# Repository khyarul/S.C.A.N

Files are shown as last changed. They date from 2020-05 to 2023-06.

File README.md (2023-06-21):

# S.C.A.N
 Small and Cheap Attendance Node

## Attendance Node Machine
   - Hardware: ESP8266 Wemos D1 Mini - Software: Arduino C/C++

   - Feature and library used:
     - [x] Dual Mode: **Tap to Unlock Door** and **Attendance Mode**
     - [x] Scheduler.h (Multitask) from [Here](https://github.com/nrwiersma/ESP8266Scheduler)
     - [x] PubSubClient.h (MQTT protocol client)
     - [x] LiquidCrystal_I2C.h (LCD16x2 I2C)
     - [x] MFRC522.h (RFID SPI module 13.56MHz)
     - [x] ArduinoOTA.h (wireless/no-usb programming)
     - [x] Reed/magnetic sensor for Door state
     - [x] solenoid door lock port max. 12V/1A (12W)
     - [x] 5V/3A (15W) power supply input
   
   - Recommended ESP8266 Wemos D1 Mini Arduino Configuration:
   
   arduino config
 
   - Wemos D1 Mini Port Allocation:
   
 PORT |	FUNCTION |	DEVICE
 -----|----------|-------   
 D1 |	I2C SCL |	LCD 16x2
 D2 |	I2C SDA |	LCD 16x2
 D4 |	SPI Reset |	RC522
 D5 |	SPI SCK |	RC522
 D6 |	SPI MISO |	RC522
 D7 |	SPI MOSI	| RC522
 D8 |	SPI SS	| RC522
 D0 |	Digital Output	| Solenoid
 TX |	Digital Input	| Attendance Mode button
 RX |	Digital Output |	Buzzer
 D3 |	Digital Input |	“Unlock Door” Mode button
 A0 |	Analog Input |	Magnetic Switch/Sensor

   - Mechanic Documentation Photo:
     - **Acrylic Case for LCD, RFID sensor, button, and buzzer. Install it outside the room.**



     - **Acrylic case for controller part, reed/magnet sensor and solenoid port. Install it inside the room.**


     - **Solenoid port and small hole for reed/magnet sensor wire**



   
## GUI (Node Monitor & Employee Manager)
- Tested on Windows 10 PC and Ubuntu Mate 18.04 64bit on Raspberry Pi 3 (Should be supported with Ubuntu 64bit on PC)
- Main file: **"SCAN_node_monitor.py"** (**"karyawan.py"**, **"icons"**, and **"images" need to be in the same folder**)

- Feature:
  - [x] Manage & monitor all Node Machine that connected to the same MQTT server.
  - [x] Using MongoDB database for Node & Employee Manager.
  - [x] Unlock door on every Node Machine remotely.

- Python 3.7 module/library used:
  - [x] Pyqt5 (for GUI)
  - [x] PyMongo (for MongoDB Database driver)
  - [x] Paho-Mqtt (MQTT client)
  - [x] Threading (Multitasking using Multithreading, 1 thread per 1 Attendance Node Machine)

## Support & DONATE this open source project:
  - PAYPAL  : [SentinelCreative](https://www.paypal.me/sentinelcreative "PAYPAL")
  - BNI     : 1284959883 (Khyarul Arham)
  - Jago    : 504120557241 (Khyarul Arham)

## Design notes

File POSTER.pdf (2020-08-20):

# PENERAPAN MOSQUITTO SEBAGAI SERVER MQTT LOKAL PADA KOMUNIKASI ANTARA DATABASE MONGODB DAN MESIN ABSENSI MULTI-NODE

1. Menerapkan protokol MQTT pada mesin absensi di local area network dengan mengandalkan access point terdekat untuk komunikasi lebih handal dan aman.
2. Menerapkan algoritma komunikasi bidirectional dari protokol MQTT pada perangkat-perangkat yang terhubung pada jaringan lokal atau jaringan publik.
3. Menggunakan aplikasi GUI designer PyQt5 dan penerapannya untuk menginput, mengedit, dan menampilkan data dari suatu database dengan konsep NoSQL salah satunya MongoDB dengan library PyMongo pada Python serta sebagai penerapan manajemen database secara terpusat.
4. Menganalisa pengaruh penggunaan server MQTT (lokal dan publik), proses parsing data pada Python dan update pada database MongoDB, serta penambahan jumlah client terhadap delay pada sistem.

Mesin absensi di pasaran rata-rata hanya menggunakan sistem standalone database, yaitu 1 database untuk 1 mesin walaupun sudah menerapkan prinsip IoT. Salah satu protokol yang sering digunakan dalam IoT saat ini salah satunya protokol MQTT. Protokol MQTT sudah sering dijadikan pembahasan, namun masih memanfaatkan public MQTT Server yang sudah siap pakai dan kebanyakan hanya dilakukan untuk komunikasi 1 arah. Public MQTT broker harus menggunakan internet walaupun hanya untuk perangkat yang letaknya tidak terlalu jauh. Komunikasi antar client dengan cloud broker akan terganggu bila koneksi internet mengalami gangguan terutama instansi yang berada di daerah yang belum dijangkau oleh ISP yang handal. Untuk mengatasinya perlu menerapkan MQTT menggunakan jaringan lokal yang sudah tersedia tanpa memerlukan internet. Dengan menerapkan protokol MQTT secara lokal dan komunikasi dua arah, PyQt serta MongoDB sebagai manajemen database terpusat diharapkan mempermudah dalam memonitor dan mengatur jumlah mesin absensi yang terkoneksi.

Urutan kerja sistem autentikasi dari Client Node ke Client Database, yaitu:
1. User melakukan tapping RFID tag pada mesin client node. Mesin akan mengirimkan UID ke server MQTT melalui topik khusus UID dan unique client ID dari node bersangkutan.
2. Client database akan mendeteksi payload yang masuk di topik tersebut. Dengan syarat client database sudah berlangganan ke topik tersebut.
3. Data yang diterima oleh client database akan dilakukan parsing serta pengecekan ke database MongoDB.
4. Client database akan mengirim respon balik ke server MQTT sesuai topik dari client ID node yang bersangkutan apakah UID user memiliki akses atau tidak.
5. Client node akan menampilkan output dan respon ke user berdasarkan payload respon yang sudah diterima oleh client node.
- Local MQTT Server
1. Hardware: Raspberry Pi 3 Model B V1.2
2. Sistem Operasi: Ubuntu Mate 18.04.4 LTS 64bit
- Monitor dan Database Client
1. Hardware: Raspberry Pi 3 Model B V1.2
2. Sistem Operasi: Ubuntu Mate 18.04.4 LTS 64bit
3. Bahasa Pemrograman: Python 3.6
4. GUI: PyQt5
5. Database: MongoDB V4.2
6. Database library: Pymongo
7. MQTT Client library: Paho-Mqtt
- Node Client
1. Hardware: ESP8266 Wemos D1 Mini
2. Bahasa Pemrograman: Arduino C/C++
TUJUAN | LATAR BELAKANG
CARA KERJA ALAT | SPESIFIKASI ALAT | BLOK DIAGRAM HARDWARE NODE CLIENT
FLOWCHART SISTEM AUTENTIKASI | BLOK DIAGRAM SISTEM KOMUNIKASI

### Dibuat Oleh: Khiarul Arham

(1903423002)

### Dosen Pembimbing:

Agus Wagyana, S.T., M.T.
(196808241999031002)

### Tanggal Sidang: 28 Juli 2020

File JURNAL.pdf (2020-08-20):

PENERAPAN MOSQUITTO SEBAGAI SERVER MQTT LOKAL PADA KOMUNIKASI ANTARA DATABASE MONGODB DAN MESIN ABSENSI MULTI-NODE Khiarul Arham, Agus Wagyana Politeknik Negeri Jakarta, Jurusan Teknik Elektro, Prodi Broadband Multimedia Jl. Prof. Dr. G. A. Siwabessy, Kampus UI, Depok 16425 email: kh.arham@gmail.com

ABSTRACT
Attendance machines on the market mostly only use a standalone database system, which is 1 database for 1 machine despite applying the IoT principle. One protocol that is often used in IoT is the MQTT protocol. The MQTT protocol has often been studied, but it still utilizes public MQTT Servers that are ready to use and most are only done for 1-way communication. Public MQTT brokers must use the internet even if only for devices that are not too far away. Communication between clients and public brokers will be disrupted if the internet connection is interrupted, especially agencies in areas that have not been reached by a reliable ISP. To overcome this, it is necessary to implement MQTT using a local network that is already available without the need for internet. By implementing the MQTT protocol locally and two-way communication, PyQt and MongoDB as a centralized database management are expected to make it easier to monitor and manage the number of connected attendance machines. The system applied in this study has 3 components, namely MQTT Server, Monitor and Database Client, and Node Client. To conduct two-way communication each client publishes and subscribes to specific topics based on the client ID. Next will be investigated the effect of 3 parameters, i.e. the type of MQTT server used, the number of client nodes, and the process of updating the database to the delay in the authentication process. Obtained the difference in delay between the application of local and public MQTT servers is 816.75 ms. Increasing the number of client nodes also affects the delay of about 135.75 ms for each addition of 1 node client. The process of updating the MongoDB database in Python has the least delay effect compared to 2 other parameters, which is only 68.75 ms.

Key words: Attendance; client monitor; client node; MongoDB; Mosquitto; MQTT; PyQt

ABSTRAK
Mesin absensi di pasaran rata-rata hanya menggunakan sistem standalone database, yaitu 1 database untuk 1 mesin walaupun sudah menerapkan prinsip IoT. Salah satu protokol yang sering digunakan dalam IoT saat ini salah satunya protokol MQTT. Protokol MQTT sudah sering dijadikan pembahasan, namun masih memanfaatkan public MQTT Server yang sudah siap pakai dan kebanyakan hanya dilakukan untuk komunikasi 1 arah. Public MQTT broker harus menggunakan internet walaupun hanya untuk perangkat yang letaknya tidak terlalu jauh. Komunikasi antar client dengan cloud broker akan terganggu bila koneksi internet mengalami gangguan terutama instansi yang berada di daerah yang belum dijangkau oleh ISP yang handal. Untuk mengatasinya perlu menerapkan MQTT menggunakan jaringan lokal yang sudah tersedia tanpa memerlukan internet.

Dengan menerapkan protokol MQTT secara lokal dan komunikasi dua arah, PyQt serta MongoDB sebagai manajemen database terpusat diharapkan mempermudah dalam memonitor dan mengatur jumlah mesin absensi yang terkoneksi. Sistem yang diterapkan pada penelitian ini memiliki 3 komponen, yaitu MQTT Server, Monitor dan Database Client, dan Node Client. Untuk melakukan komunikasi dua arah setiap client melakukan publish dan subscribe ke topik tertentu berdasarkan client ID. Selanjutnya akan dicari tahu pengaruh 3 parameter, yaitu jenis server MQTT yang digunakan, jumlah client node, dan proses update database terhadap delay dalam proses autentikasi. Didapatkan perbedaan delay antara penerapan server MQTT lokal dan publik adalah 816.75 ms. Bertambahnya jumlah client node juga mempengaruhi delay sekitar 135.75 ms setiap penambahan 1 client node. Proses update database MongoDB pada Python memiliki pengaruh delay paling kecil dibandingkan 2 paramater lain, yaitu hanya 68.75 ms.

Kata kunci: Attendance; client monitor; client node; MongoDB; Mosquitto; MQTT; PyQt

PENDAHULUAN
Sistem absensi seringkali menjadi
perhatian | sebuah | instansi | dalam
pengelolaan puluhan atau bahkan ratusan sumber daya manusia (karyawan), sehingga banyak perusahaan telah menerapkan sistem absensi digital. Kebanyakan instansi atau perusahaan memiliki gedung yang berdekatan atau hanya satu gedung, sehingga cukup meletakkan 1 atau 2 mesin absensi dengan pengumpulan data manual
menggunakan | flashdisk | tanpa | harus
mengintegrasikannya ke jaringan lokal instansi tersebut. Beda halnya dengan instansi dengan area yang luas dan jarak antar gedung yang cukup jauh, sehingga mengharuskan instansi tersebut memasang mesin absensi di masing-masing gedung tempat karyawan bekerja yang jumlahnya tidak sedikit. Tentunya sangat merepotkan untuk mengumpulkan data di tempat-tempat yang berjauhan secara manual untuk masing-masing mesin. Kalaupun masing-
masing | gedung | memiliki | seorang
perwakilan untuk mengumpulkan datanya, maka untuk menggabungkan semua data
tersebut | akan | merepotkan | bagian
administrasi bila dilakukan setiap hari atau setiap minggu.
Untuk mesin yang memiliki fitur logging ke jaringan sendiri masih terbilang cukup mahal dan rata-rata memiliki database yang terpisah (standalone), yang beredar di pasaran misalnya ZT1200 atau ZT1100 yang menggunakan MySQL sebagai standalone database. Bagi instansi sejenis pabrik, manufaktur, atau bisnis dengan kemampuan budget tinggi, itu bukanlah masalah besar. Namun untuk instansi non-bisnis dengan kemampuan budget menengah atau instansi pada umumnya, dan ditambah dengan area luas, hal itu benar-benar harus dipertimbangkan. Oleh karena itu masih banyak yang
menggunakan | cara | manual | untuk
perekapan data absensi.
| Sekarang | ini | dengan | adanya
perkembangan | sistem | integrasi | antar
perangkat dengan jaringan seperti Internet
of | Things | (IoT) | ditambah | dengan
penerapannya yang tidak hanya pada komputer atau perangkat jaringan pada umumnya. Begitu mudahnya sekarang ini dalam menemukan source code atau binary resource untuk berbagai macam protokol pendukung IoT yang disediakan untuk para hobby dan developer, salah satunya protokol Message Queiuing Telemetry Transport (MQTT). MQTT menjadi salah satu protokol yang banyak digunakan pada aplikasi IoT karena memiliki ukuran paket data yang kecil sehingga cocok digunakan pada aplikasi real-time atau aplikasi yang membutuhkan kemampuan data streaming yang baik. Dari beberapa info yang penulis dapatkan dari dosen dan referensi di internet, protokol MQTT sudah beberapa kali dijadikan bahan pembahasan untuk keperluan tugas akhir atau skripsi, namun masih memanfaatkan public cloud MQTT broker yang sudah siap pakai. Dalam penerapannya cloud MQTT broker harus menggunakan koneksi internet walaupun hanya untuk perangkat yang letaknya tidak
jauh | atau | berdekatan. | Tentu | akan
menghambat komunikasi antar | client
dengan cloud broker bila saat koneksi internet atau Internet Service Provider (ISP) yang sering mengalami gangguan terutama instansi yang berada di daerah tepencil atau masih belum dijangkau banyak ISP lain yang handal. Sehingga untuk mengatasinya agar lebih efisien perlu adanya penerapan MQTT yang cukup memanfaatkan jaringan lokal yang sudah tersedia di suatu instansi tanpa harus memakan bandwidth internet.
Salah | satu | penyedia | open-source
MQTT client & broker yaitu Eclipse
Mosquitto. | Dengan | menggunakan
Mosquitto kita dapat menerapkan protokol MQTT pada jaringan lokal. Mosquitto juga menyediakan binary yang mendukung berbagai macam sistem operasi seperti Windows, Linux, dan Mac. Bahkan Mosquitto juga dapat dipasang pada single board computer (SBC) seperti Raspberry Pi. Dengan memanfaatkan low power single board computer sebagai MQTT broker maka kita tidak perlu menggunakan sebuah Personal Computer (PC) yang harus standby selama koneksi dengan broker diperlukan terkait pertimbangan penggunaan daya. Selain itu output data dari client juga dapat ditampilkan pada sebuah database dengan merancang GUI pada SBC tersebut. Salah satu platform GUI yang dapat digunakan, yaitu Qt yang juga menyediakan tools designer untuk mempermudah developer saat merancang GUI dengan fitur konversi hasil desain ke
bahasa | pemrograman | seperti | C/C++
ataupun Python (PyQt).
Penerapan IoT dalam inovasi teknologi semakin menuntut adanya variasi data serta
fleksibilitas | dalam | mengakses | serta
menyimpan data. Banyak perusahaan besar di dunia seperti Facebook yang telah bermigrasi dan menerapkan database NoSQL salah satunya MongoDB. Salah satu fitur MongoDB adalah menyimpan data dalam bentuk JSON document. Sebagai programmer pada umumnya berpikir secara objek, dengan cara ini
MongoDB | mendekati | cara | berpikir
tersebut, sehingga lebih fleksibel dan handal dibandingkan database dengan pemodelan baris dan kolom seperti MySQL
dan | sejenisnya. | Dalam | akses
pemrogramannya, Python sangat cocok dipasangkan dengan MongoDB karena dalam Python memiliki tipe data dictionary yang sangat mirip dengan JSON. Ditambah dengan adanya library atau driver yang tersedia pada Python untuk mengakses MongoDB, yaitu PyMongo. Dengan begitu akan mempermudah dalam implementasi dan menggabungkannya pada sistem IoT. Tujuan dari penelitian ini adalah menerapkan protokol MQTT pada mesin absensi di local area network dengan mengandalkan access point terdekat untuk komunikasi lebih handal dan aman.
Kemudian | menerapkan | algoritma
komunikasi bidirectional dari protokol MQTT pada perangkat-perangkat yang terhubung pada jaringan lokal atau jaringan
publik. | Menggunakan | aplikasi | GUI
designer PyQt5 dan penerapannya untuk menginput, mengedit, dan menampilkan data dari suatu database dengan konsep NoSQL salah satunya MongoDB dengan library PyMongo pada Python serta sebagai penerapan manajemen database secara terpusat. Terakhir adalah menganalisa pengaruh penggunaan server MQTT (lokal dan publik), proses parsing data pada
Python | dan | update | pada | database
MongoDB, serta penambahan jumlah client terhadap delay pada sistem.

METODE PENELITIAN
Alat yang akan dirancang berupa sistem
absensi | multi-node | dengan | database
terpusat, yaitu terdapat banyak perangkat sebagai titik pengambilan data namun
dengan | tempat | penyimpanan | serta
manajemen dan monitor terpusat dari satu perangkat saja. Sistem yang akan dirancang terdiri atas 3 komponen, yaitu Local MQTT Server, Monitor dan Database Client, dan Node Client pada satu jaringan lokal atau komunikasi tanpa melalui ISP atau jaringan eksternal.
Local MQTT Server berfungsi sebagai Server MQTT yang digunakan antar Client MQTT untuk berkomunikasi atau tempat di mana fungsi "publish" dan "subscribe" akan diproses serta diatur oleh Server MQTT.
Monitor dan Database Client berfungsi untuk memonitor setiap Node Client yang terhubung dengan server MQTT yang sama serta merekam dan mengatur pengecekan data setiap node dan karyawan pada database. Pada client ini juga akan
dijalankan aplikasi GUI | yang telah
dirancang | dengan | PyQt5 | untuk
membangun fungsi monitor dan sebagai jembatan penghubung dengan database. Node Client memiliki fungsi utama sebagai titik absensi. Node Client tidak dapat beroperasi bila Client Monitor dan Database tidak dijalankan walaupun Node Client sudah terkoneksi ke server. Fungsi opsional yaitu sebagai sistem pengunci pintu sekaligus membaca kondisi pintu terbuka atau tertutup. Kedua fungsi ini juga akan dimonitor oleh Client Monitor dan Database. Untuk mendukung kedua fungsi ini user dapat memilih apakah ingin menggunakan mode untuk membuka pintu (secara default) atau menggunakan mode presensi kehadiran.
Pada mode membuka pintu tidak akan dilakukan update data ke database, namun hanya terjadi proses autentikasi. Sedangkan untuk sistem kehadiran akan dilakukan update data ke database dan direkam berdasarkan pola 2 waktu, yaitu datang dan pulang per harinya untuk setiap user.

Bagian kontroler Node Client akan diinstalasi di dalam ruangan, sedangkan bagian interface dan scanner berada di luar. Hal ini untuk mendukung fungsi Node Client sebagai sistem pengaman suatu ruangan. Namun yang terpenting Node Client harus dapat menjangkau access point terdekat.
Untuk | mempermudah | dalam
memahami dan merealisasikan sistem, maka akan dibuat beberapa diagram blok di antaranya diagram blok hardware (Gambar
1) dan sistem komunikasi alat (Gambar 2).

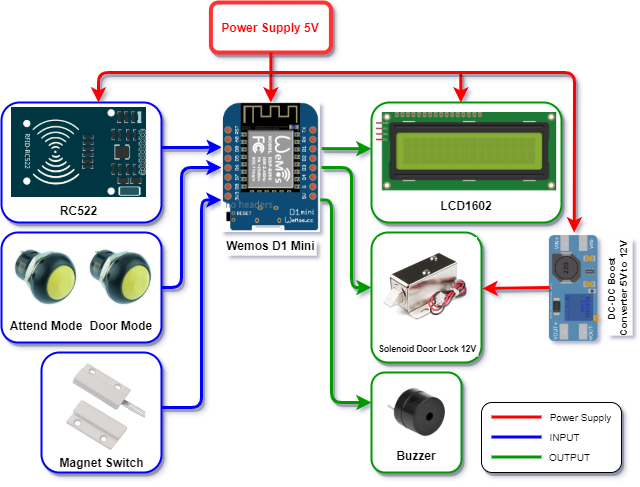
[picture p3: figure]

Gambar 1. Diagram Blok Hardware

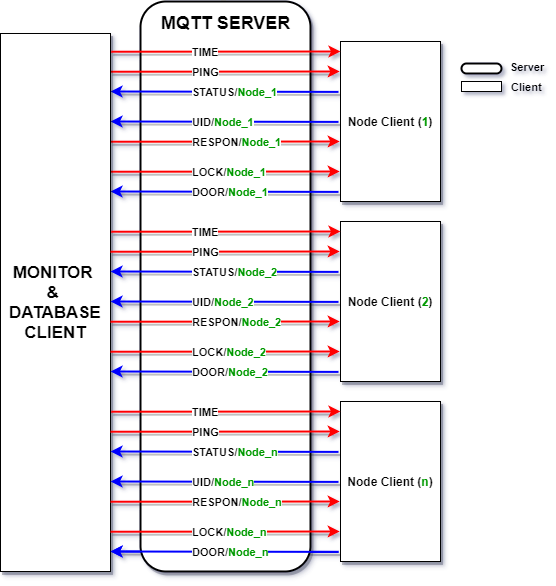
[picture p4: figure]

Gambar 2. Diagram Blok Sistem Komunikasi Alat

Sistem komunikasi terdiri dari MQTT Server dan Client. Setiap client node akan berkomunikasi dengan client monitor dan database melalui server MQTT. Proses pengiriman data antar client dilakukan melalui topik yang telah dirancang sesuai Gambar 3.2. Dapat dilihat bahwa tanda panah biru merupakan topik yang di-subscribe oleh client monitor atau di-publish oleh client node. Sedangkan tanda panah merah merupakan topik yang di-publish oleh client monitor atau di-subscribe oleh client node. Arah tanda panah menunjukkan arah publish dari dan ke.
Terdapat 2 jenis topik dari sistem yang akan dibangun, yaitu general topic dan specific topic.
1. General Topic
Merupakan topik yang digunakan untuk mem-publish data yang berlaku untuk semua client node, tanpa membedakan client ID, dan tidak memiliki sub-topic, serta semua client node berlangganan ke topik tersebut. Hanya 2 general topic yang digunakan pada sistem ini, yaitu “PING” dan “TIME” yang akan di-publish dengan interval waktu tertentu. Dengan kata lain topik ini bersifat broadcast.
- “PING”: | Digunakan | untuk
mengecek koneksi setiap client node.
- “TIME”: | Digunakan | untuk
mengirim waktu ke setiap client node.
2. Specific Topic
Merupakan topik yang hanya berlaku untuk client node tertentu berdasarkan client ID, topik memiliki karakter pemisah “/” dengan sub-topic, dan hanya client node dengan client ID bersangkutan yang melakukan publish ataupun subscribe ke topik tersebut. Client ID akan digunakan sebagai sub-topic. Pada perancangan sistem kali ini digunakan client ID dengan format “Node_n”. Di bawah ini merupakan specific topic yang digunakan dalam sistem:
- “STATUS/Node_n”: Client node yang aktif akan mengirim respon ke topik ini setelah menerima data yang berasal dari topik “PING”.
Client | node | yang | merespon
dianggap aktif atau terkoneksi dengan server. Khusus pada topik ini masing-masing client node menggunakan fitur “Last Will Message” jika suatu waktu koneksi terputus. Message ini akan disimpan oleh server MQTT dan akan
diteruskan ke subscriber topik ini yaitu client monitor jika salah satu publisher dalam hal ini client node
bersangkutan | tiba-tiba | terputus
koneksi dengan server.
- “UID/Node_n”: Digunakan dalam proses autentikasi oleh client node dengan cara mengirim data dengan
format | “MODE:KODE | RFID
TAG” ke | client monitor setelah
user melakukan tapping.
- “RESPON/Node_n”: Setelah client monitor mendapat data dari topik “UID/Node_n” client monitor akan melakukan proses autentikasi ke database. Hasil dari proses ini
akan | dikirim | ke | client node
bersangkutan | melalui | topik
“RESPON/Node_n”.
- “LOCK/Node_n”: Digunakan oleh client monitor untuk membuka kunci (mengaktifkan solenoid) pada client node bersangkutan.
- “DOOR/Node_n”: Digunakan oleh client node untuk mengirim status
pintu | (terbuka | atau | tertutup)
berdasarkan state yang terbaca oleh magnetic switch. Client node akan mengirim data pada topik ini hanya pada saat pertama kali menyala dan pada saat status pintu berubah (dari
terbuka | menjadi | tertutup | atau
sebaliknya).

Berikutnya adalah merancang layout aplikasi yang dinamis. Ada 2 aplikasi yang akan dibuat, yaitu “S.C.A.N – Node Monitor” (Gambar 3) dan “S.C.A.N – Employee Manager” (Gambar 4).

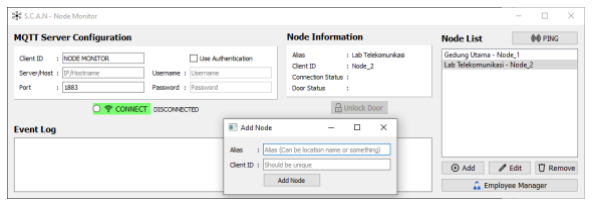
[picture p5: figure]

Gambar 3. S.C.A.N – Node Monitor

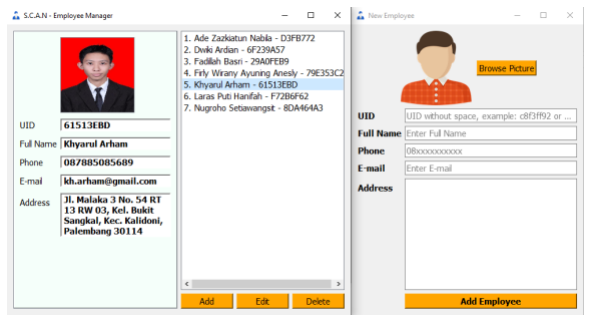
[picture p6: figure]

Gambar 4. S.C.A.N – Employee Manager

Aplikasi Node Monitor berfungsi untuk:
- Memonitor status koneksi dan kondisi pintu setiap client node.
- Merekam aktivitas user di setiap
client | node | dengan | cara
menampilkannya ke Event Log.
- Mendukung | fungsi | Create,
Read, Update, Delete (CRUD) pada Node List ke database MongoDB, serta mempermudah pengaturan koneksi ke server MQTT dengan adanya menu
MQTT Server Configuration.

Sedangkan aplikasi Employee Manager berfungsi untuk mempermudah dalam manajemen dan membangun fungsi CRUD pada data user ke database MongoDB.

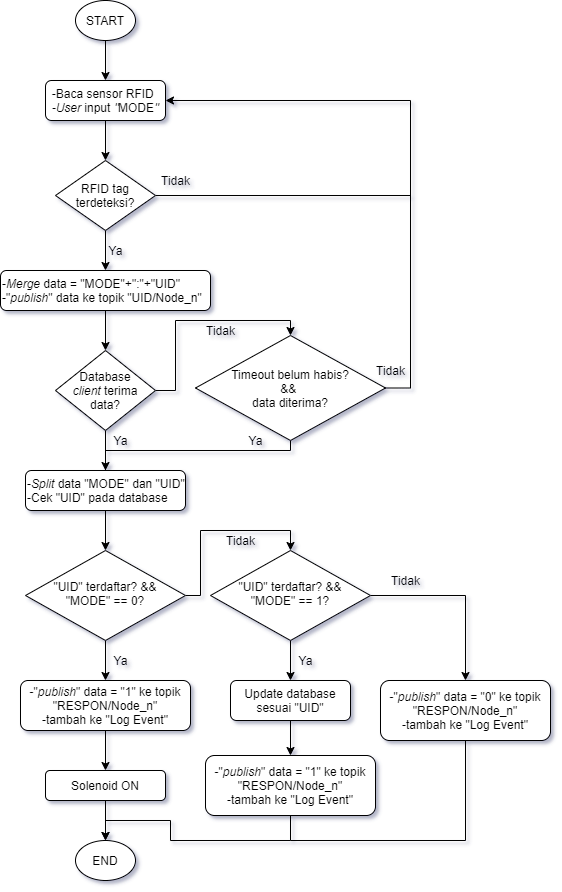
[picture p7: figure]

Gambar 5. Flowchart Sistem Autentikasi

Dari flowchart (Gambar 5) dapat dijabarkan proses autentikasi pada sistem sebagai berikut:

1. User menggunakan tombol pada mesin client node untuk memilih MODE 0 (membuka kunci pintu) atau MODE 1 (presensi).
2. Setelah user melakukan tapping, kode RFID (UID) dan mode akan di-merge menjadi satu dengan format "MODE:UID", lalu client node mem-
publish | data | tesebut | ke | topik
"UID/Node_n" dengan "Node_n" adalah client ID dari client node bersangkutan.
3. Bila data pada topik "UID/Node_n" belum diterima oleh client monitor selama waktu tertentu, maka user harus mengulang dari langkah 1.

4. Setelah diterima oleh client monitor data "MODE" dan "UID" akan dipecah lagi.
5. Jika UID terdaftar dan MODE = 0, maka client monitor akan mengirim
karakter | "1" | pada | topik
"RESPON/Node_n" dan menambah data ke Log Event, sehingga pengunci pintu pada client node bersangkutan akan terbuka (Solenoid ON).
6. Jika UID terdaftar dan MODE = 1, maka client monitor akan meng-
update | tanggal | dan jam | pada
document | database | dari | user
bersangkutan | terlebih | dahulu
(disimpan | dengan | format
{"tanggal":["waktu
hadir":"waktu pulang"]} ), baru mengirim karakter "1" pada topik "RESPON/Node_n" dan menambah data ke Log Event.
7. Jika UID tidak terdatar di database,
client | monitor | akan | langsung
mengirim karakter "0" ke topik "RESPON/Node_n", sehingga client node akan memberitahu user pada LCD bahwa UID tidak dikenal atau tidak terdaftar. Terakhir pada Log Event akan muncul notifikasi UID tidak dikenal.

Setelah semua selesai dikonfigurasi dan dijalankan, tahap selanjutnya adalah proses tapping kartu RFID pada Client Node. Pengukuran dilakukan terhadap variasi berikut:

Tabel 1. Variasi Percobaan

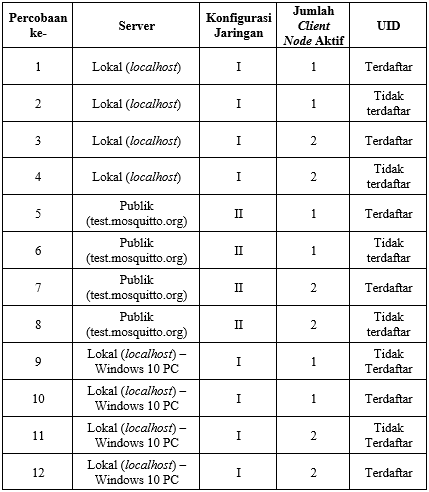
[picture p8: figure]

Khusus UID terdaftar menggunakan
“61513EBD” | dengan | nama | pemilik
“Khyarul Arham”, sedangkan UID yang tidak terdaftar pada database menggunakan “D3FB772” yang akan terdeteksi sebagai “Unknown UID”.
Variasi 1-4 Raspberry Pi difungsikan sebagai server dan tempat dijalankannya aplikasi Node Monitor dan Employee Manager. Sedangkan khusus variasi 9-12 server dan aplikasi dijalankan melalui PC dengan OS Windows 10 untuk melakukan perbandingan delay terhadap variasi 1-4. Sedangkan variasi 5-8 menggunakan server MQTT publik dengan aplikasi Node Monitor dan Employee Manager tetap dijalankan pada Raspberry Pi.

HASIL DAN PEMBAHASAN
Data pengukuran diambil dari “Event Log” pada aplikasi Node Monitor yang
telah | dirancang. | Setiap | percobaan
dilakukan sebanyak 17 kali dengan variasi berdasarkan Tabel 1. Berikut tabel hasil pengukuran berdasarkan tabel variasi percobaan.

Tabel 2. Hasil Pengukuran Delay (ms) Proses Autentikasi (Raspberry Pi)

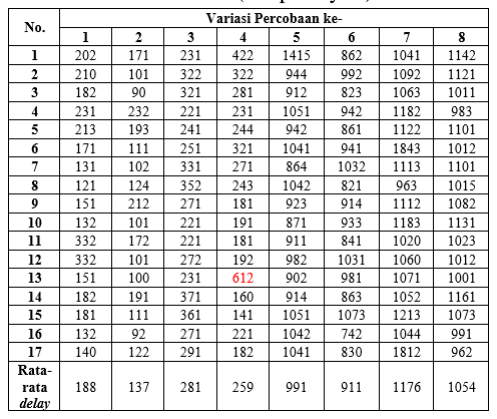
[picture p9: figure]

Tabel 3. Hasil Pengukuran Delay (ms) Proses Autentikasi (Windows 10 PC)

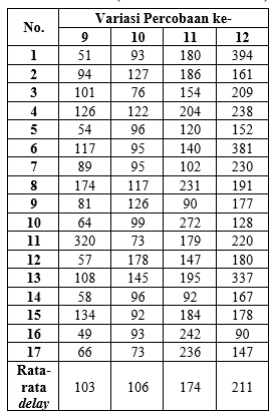
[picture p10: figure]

### 1. Pengaruh Proses Update Database

Tahap pertama adalah mencari tahu selisih delay pada saat menggunakan server dan jumlah client node aktif yang sama, namun hanya jenis UID yang berbeda, yaitu terdaftar dan tidak terdaftar pada database. Selisih ini dapat dihitung pada percobaan variasi antara:
- 1 dan 2: selisih rata-rata delay = 188-137 = 51 ms
- 3 dan 4: selisih rata-rata delay = 281-259 = 22 ms
- 5 dan 6: selisih rata-rata delay = 991-911 = 80 ms
- 7 dan 8: selisih rata-rata delay = 1176-1054 = 122 ms

Pada variasi 1, 3, 5, dan 7 dari tabel hasil pengukuran diketahui selalu memiliki
rata-rata | delay | yang | lebih | besar
dibandingkan dengan variasi 2, 4, 6, dan 8. Hal ini dikarenakan variasi 1, 3, 5, dan 7 menggunakan UID yang terdaftar pada database, sedangkan variasi 2, 4, 6, dan 8 menggunakan UID yang tidak terdaftar pada database. UID yang terdaftar akan melalui proses query dan update database
MongoDB | dalam | program | Python,
sedangkan UID yang tidak terdaftar hanya melalui proses query tanpa perlu dilakukan update data pada database MongoDB. Jika UID yang bersangkutan tidak match (tidak terdaftar), aplikasi Node Monitor akan langsung mem-publish karakter “0” pada topik “RESPON/clientID”. Dari selisih rata-rata delay di atas, maka didapat waktu yang diperlukan oleh MongoDB dengan Python pada sistem ini untuk meng-update database:
Rata − rata Waktu Update Database
| =

51 + 22 + 80 + 122
| | | 4
= 68.75 ms

Perintah update database pada kode program Python untuk aplikasi Node
Monitor, | | | | yaitu
“employeeCollection.update_one(query, newValue)”. Kode ini dipanggil hanya ketika UID yang diterima oleh aplikasi Node Monitor cocok atau terdapat pada database (UID terdaftar pada database).
Respon | bahwa | UID | terdaftar | dan
autentikasi | sukses | ditandai | dengan
dijalankannya | perintah
“client.publish('RESPON/' | + | clientID,
name)” untuk mengirim nama dari pemilik UID tersebut.

### 2. Pengaruh Jumlah Client Node yang

Aktif
Tahap selanjutnya adalah mencari tahu selisih delay pada saat menggunakan server dan tipe UID (antara terdaftar atau tidak terdaftar) yang sama, namun hanya jumlah client node aktif saja yang berbeda. Selisih ini dapat dihitung pada percobaan variasi antara:
- 3 dan 1: selisih rata-rata delay = 281-188 = 93 ms
- 4 dan 2: selisih rata-rata delay = 259-137 = 122 ms
- 7 dan 5: selisih rata-rata delay = 1176-281 = 185 ms
- 8 dan 6: selisih rata-rata delay = 1054-911 = 143 ms

Pada variasi 3, 4, 7, dan 8 dari tabel hasil pengukuran diketahui selalu memiliki
rata-rata | delay | yang | lebih | besar
dibandingkan dengan variasi 1, 2, 5, dan 6. Hal ini dikarenakan variasi 1, 2, 5, dan 6
aplikasi | Node | Monitor | hanya
berkomunikasi dengan hanya 1 client node aktif, sedangkan variasi 3, 4, 7, dan 8 aplikasi Node Monitor berkomunikasi dengan 2 client node aktif. Semakin banyak client node maka aplikasi harus membuat lebih banyak thread untuk meng-handle masing-masing client node. Dari selisih rata-rata delay di atas, maka didapat pengaruh jumlah client node aktif terhadap
waktu | yang | diperlukan | saat | proses
autentikasi pada sistem ini:

Delay/penambaℎan client node =

93 + 122 + 185 + 143
4
= 135.75 ms/penambahan client node

Namun hasil delay dari pengaruh penambahan jumlah client node aktif ini belum diketahui apakah akan meningkat secara linier atau non-linier. Untuk mengetahuinya harus dilakukan pengujian dengan lebih dari 2 client node.

### 3. Pengaruh Server yang Digunakan

Tahap berikutnya adalah mencari tahu delay dengan cara membandingkan 2 variasi saat beroperasi dengan jumlah client node dan tipe UID (antara terdaftar atau

tidak | terdaftar) | yang | sama, | namun
menggunakan server MQTT yang berbeda (antara server lokal hasil rancangan dan server publik). Selisih ini dapat dihitung pada percobaan variasi antara:
- 5 dan 1: selisih rata-rata delay = 991-188 = 803 ms
- 6 dan 2: selisih rata-rata delay = 911-137 = 774 ms
- 7 dan 3: selisih rata-rata delay = 1176-281 = 895 ms
- 8 dan 4: selisih rata-rata delay = 1054-259 = 795 ms

Pada variasi 5, 6, 7, dan 8 hasil pengukuran delay lebih besar dibandingkan dengan variasi 1, 2, 3, dan 4. Ini disebabkan variasi 5, 6, 7, dan 8 menggunakan server MQTT publik dan membutuhkan koneksi internet untuk mengirim dan menerima data. Sedangkan pada variasi 1, 2, 3, dan 4 sudah menggunakan server MQTT lokal yang telah dirancang, sehingga pengiriman data tidak melalui internet dan tentunya akan menekan waktu yang diperlukan dalam proses autentikasi. Dengan begitu dapat dihitung delay antara penerapan server MQTT lokal dengan server MQTT publik pada sistem ini:

DelayMQTT publik−MQTT lokal =

803 + 774 + 895 + 795
| | | 4
= 816.75 ms

### 4. Pengaruh Perbedaan Spesifikasi

Perangkat
Pada bagian ini dikhususkan untuk percobaan variasi 9-12 yang menggunakan PC dengan OS Windows 10. Berdasarkan tabel 4.3 bila dibedakan dengan percobaan variasi 1-4, maka dapat dibandingkan nilainya:
- 2 dan 9: selisih rata-rata delay = 137-103 = 34 ms
- 1 dan 10: selisih rata-rata delay = 188-106 = 82 ms
- 4 dan 11: selisih rata-rata delay = 259-174 = 85 ms

- 3 dan 12: selisih rata-rata delay = 281-211 = 70 ms

Pada variasi 1-4 hasil pengukuran delay selalu lebih besar dibandingkan percobaan variasi 9-12 yang menggunakan PC sebagai server dan dijalankannya aplikasi Node Monitor dan Employee Manager. Dengan begitu dapat diketahui selisih delay antara penerapan PC dan mini PC:

DelayRaspi−PC | =

34 + 82 + 85 + 70
4
= 67.75 ms

Dari hasil di atas ada beberapa faktor lain yang juga memungkinkan dapat
mempengaruhi | hasil | pengukuran | di
antaranya resource dan spesifikasi pada hardware itu sendiri. Misalnya pada variasi percobaan ke-4 no. 13 terukur lonjakan delay cukup besar, yaitu 612 ms, penyebab spesifik belum bisa diketahui, namun diduga bisa terjadi karena spesifikasi RAM yang rendah pada server (Raspberry Pi 3B): DDR2 900MHz dengan kapasitas yang kecil, yaitu 1 GB. Berbeda dengan
komputer | pada | umumnya | yang
menggunakan | DDR3 | yang | tentunya
beberapa kali lipat lebih cepat dibanding RAM tipe DDR2. Ditambah lagi pada aplikasi S.C.A.N – Node Monitor yang
telah | dirancang | menerapkan | fitur
multithread untuk meng-handle banyak
client | node | yang | tentunya | akan
membutuhkan banyak alokasi memori RAM. Hal yang paling berpengaruh terhadap lonjakan delay, yaitu banyaknya thread yang dijalankan pada mesin node client sendiri. Sebab ESP8266 sendiri memiliki kecepatan dan memori yang sangat kecil.

KESIMPULAN
Dari percobaan dan pengukuran serta analisa yang telah dilakukan maka dapat ditarik kesimpulan sebagai berikut:
1. Penggunaan server MQTT lokal dapat mengurangi delay proses pengiriman data dibandingkan server
MQTT | publik. | Pada | proses
autentikasi UID dalam sistem ini penggunaan server MQTT lokal memiliki waktu rata-rata 816.75 ms lebih cepat dibandingkan server MQTT publik.
2. Bertambahnya jumlah client node
yang | aktif | akan | membuat
bertambahnya delay saat proses autentikasi, apakah itu menggunakan server lokal maupun server publik.
Dari | pengujian | didapatkan
peningkatan delay, yaitu 135.75 ms setiap penambahan 1 client node.
3. Proses update database memiliki pengaruh paling kecil terhadap delay
dalam | proses | autentikasi
dibandingkan pengaruh penggunaan server MQTT (antara lokal atau
publik) | ataupun | pengaruh
bertambahnya jumlah client node. Pada sistem ini didapat lamanya waktu rata-rata yang diperlukan untuk meng-update data dengan MongoDB adalah hanya 68.75 ms.
4. Perbedaan perangkat yang digunakan mempengaruhi performa saat proses autentikasi. Dari pengujian antara Raspberry Pi Ubuntu Mate 18.04 dan
PC | Windows | 10 | didapatkan
perbedaan delay, yaitu 67.75 ms.

DAFTAR PUSTAKA
[1]Antonić, A., M. Marjanović, P. Skočir, and I. P. Žarko. (2015). Comparison of the CUPUS Middleware and MQTT Protocol for Smart City Services. In 2015 13th International Conference on Telecommunications (ConTEL), 1–8. doi:10.1109/ConTEL.2015.7231225. [2]Atmoko, Rachmad Andri. (2019). Dasar
Implementasi | Protokol | MQTT

Menggunakan Python dan NodeMCU. Blitar: Mokosoft Media.
[3]Bellavista, Paolo, Carlo Giannelli, and
Riccardo | Zamagna. | (2017). | The
Pervasive Environment Sensing and Sharing Solution. Sustainability 9 (4):
585. doi:10.3390/su9040585. [4]Fremantle, P., B. Aziz, J. Kopecký, and
P. Scott. (2014). Federated Identity and Access Management for the Internet of
Things. | In | 2014 | International
Workshop on Secure Internet of
Things, | 10–17.
doi:10.1109/SIoT.2014.8.
[5]IdCloudHost. (2017, Juli 7). Mengenal
Lebih | Dekat | Tentang | Database
MongoDB. Januari 23, 2019. https://idcloudhost.com/mengenal-lebih-dekat-tentang-database-mongodb/
[6]Light, R.A. (2017). Mosquitto: server and client implementation of the MQTT protocol. Journal of Open
Source | Software, | 2(13), | 265,
doi:10.21105/joss.00265.
[7]R. P Padhy, M. R. Patra, S. C. Satapathy.
(2011). | RDBMS | to | NoSQL:
Reviewing Some | Next-Generation
Non-Relational | Database’s.
International Journal of Advance
Engineering | Sciences | and
Technologies. Vol. 11, Issue No. 1, 015-030.
[8]Riverbank Computing Limited. What is Pyqt?. Januari 23, 2019.
https://www.riverbankcomputing.com/software/pyqt/intro
[9]Sasaki, Y., Yokotani, T., & Mukai, H. (2019). MQTT over VLAN for Reduction of Overhead on Information
Discovery. | 2019 | International
Conference | on | Information
Networking | (ICOIN).
doi:10.1109/icoin.2019.8718125. [10]Schulz, M., F. Chen, and L. Payne. (2014). Real-Time Animation of

Equipment in a Remote Laboratory.
In | 2014 | 11th | | International
Conference on Remote Engineering and Virtual Instrumentation (REV), 172–76.
doi:10.1109/REV.2014.6784247. [11]Sharma, T., & Aarthy, S. L. (2016). An
automatic | attendance | monitoring
system using RFID and IOT using Cloud. 2016 Online International Conference on Green Engineering
and | Technologies | (IC-GET).
doi:10.1109/get.2016.7916851. [12]Thangavel, D., X. Ma, A. Valera, H. X. Tan, and C. K. Y. Tan. (2014). Performance Evaluation of MQTT
and | CoAP | via | a | Common
Middleware. In 2014 IEEE Ninth
International | Conference | on
Intelligent Sensors, Sensor Networks
and | Information | Processing
(ISSNIP), | 1–6.
doi:10.1109/ISSNIP.2014.6827678.

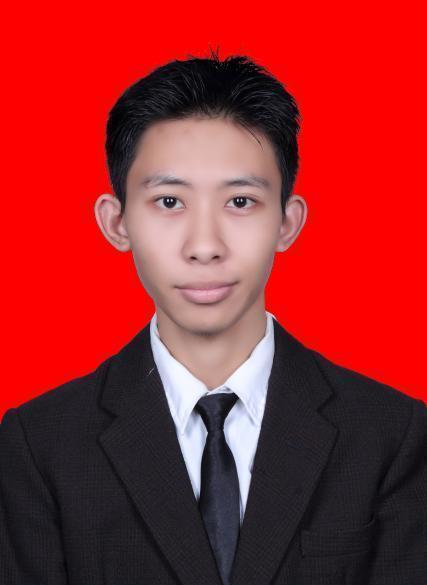
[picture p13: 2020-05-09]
GUI/images/IMG_1836__3_-removebg-preview.jpg

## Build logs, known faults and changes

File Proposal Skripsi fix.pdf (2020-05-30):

i

PROPOSAL SKRIPSI

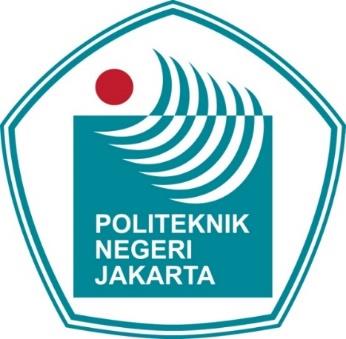
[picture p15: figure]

PENERAPAN MOSQUITTO SEBAGAI SERVER MQTT LOKAL

PADA KOMUNIKASI ANTARA DATABASE MONGODB DAN

MESIN ABSENSI MULTI-NODE

PENGUSUL:

KHIARUL ARHAM (1903423002)

PROGRAM STUDI BROADBAND MULTIMEDIA

JURUSAN TEKNIK ELEKTRO

POLITEKNIK NEGERI JAKARTA

FEBRUARI 2020

ii

LEMBAR PERSETUJUAN
CALON PEMBIMBING SKRIPSI
1. Judul | : Penerapan Mosquitto sebagai Server
| MQTT Lokal pada Komunikasi Antara
| Database MongoDB dan Mesin Absensi Multi-
| Node
2. Bentuk Tugas Akhir | : Rancang Bangun
3. Personalia Tugas Akhir
a. Nama Mahasiswa | : Khiarul Arham
NIM | : 1903423002
IPK | : -
Judul | : Penerapan Mosquitto sebagai Server
| MQTT Lokal pada Komunikasi Antara
| Database MongoDB dan Mesin Absensi Multi-
| Node
4. Perkiraan Biaya | : Rp 1.507.000
5. Alokasi Waktu Pelaksanaan | : 5 Bulan
Calon Pembimbing 1 | Calon Pembimbing 2
Agus Wagyana, S.T., M.T. | M. Fathurahman, S.T., M.T.
NIP. 196808241999031002 | NIP. 197108242003121001

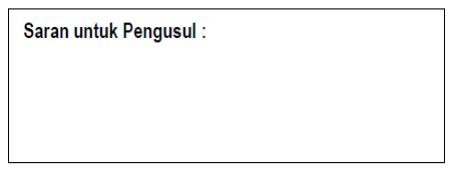
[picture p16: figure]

iii

PENILAIAN PROPOSAL SKRIPSI

JURUSAN TEKNIK ELEKTRO

JUDUL : Penerapan Mosquitto sebagai Server MQTT Lokal pada Komunikasi

Antara Database MongoDB dan Mesin Absensi Multi-Node

KRITERIA SKRIPSI

NO | KRITERIA | INDIKATOR PENILAIAN | BOBOT | SKOR | NILAI
1 | Orientasi Permasalahan Dan Pustaka | a. Latar Belakang b. Perumusan Masalah c. Tujuan d. Tinjauan Pustaka | 25
2 | Pola Penyelesaian Masalah | a. Metode Pelaksanaan Tugas Akhir | 35
3 | Fisibilitas Sumber Daya | a. Jadwal Pelaksanaan b. Personalia TA c. Perkiraan Biaya | 15
4 | Kebahasaan | a. Bahasa Proposal b. Daftar Pustaka (keserasian dan substansi kemutakhiran) | 25

Nilai Total
1. Masing-masing kriteria diberi skor 1, 2, 4, dan 5 (1=sangat kurang, 2=kurang,

4=baik, 5=sangat baik) yang mencerminkan skor seluruh butir yang dinilai

dalam masing-masing kriteria.

2. Nilai = Skor x Bobot; Nilai Total = N1+N2+N3+N4+N5
3. Hasil Penilaian : Nilai Total ≥ 400 ( Diterima ) ; Nilai Total < 400 ( Ditolak )

Depok,

Penilai

( Benny Nixon, ST., MT. )

NIP.

I. PENDAHULUAN

### 1.1 Latar Belakang

Sistem absensi seringkali menjadi perhatian sebuah instansi dalam pengelolaan

puluhan atau bahkan ratusan sumber daya manusia (karyawan), sehingga banyak

perusahaan telah menerapkan sistem absensi digital. Kebanyakan instansi atau

perusahaan memiliki gedung yang berdekatan atau hanya satu gedung, sehingga

cukup meletakkan 1 atau 2 mesin absensi dengan pengumpulan data manual

menggunakan flashdisk tanpa harus mengintegrasikannya ke jaringan lokal instansi

tersebut. Beda halnya dengan instansi dengan area yang luas dan jarak antar gedung

yang cukup jauh, sehingga mengharuskan instansi tersebut memasang mesin absensi

di masing-masing gedung tempat karyawan bekerja yang jumlahnya tidak sedikit.

Tentunya sangat merepotkan untuk mengumpulkan data di tempat-tempat yang

berjauhan secara manual untuk masing-masing mesin. Kalaupun masing-masing

gedung memiliki seorang perwakilan untuk mengumpulkan datanya, maka untuk

menggabungkan semua data tersebut akan merepotkan bagian administrasi bila

dilakukan setiap hari atau setiap minggu.

Untuk mesin yang memiliki fitur logging ke jaringan sendiri masih terbilang

cukup mahal dan rata-rata memiliki database yang terpisah (standalone), yang

beredar di pasaran misalnya ZT1200 atau ZT1100 yang menggunakan MySQL

sebagai standalone database. Bagi instansi sejenis pabrik, manufaktur, atau bisnis

dengan kemampuan budget tinggi, itu bukanlah masalah besar. Namun untuk instansi

non-bisnis dengan kemampuan budget menengah atau instansi pada umumnya, dan

ditambah dengan area luas, hal itu benar-benar harus dipertimbangkan. Oleh karena

itu masih banyak yang menggunakan cara manual untuk perekapan data absensi.

Sekarang ini dengan adanya perkembangan sistem integrasi antar perangkat

dengan jaringan seperti Internet of Things (IoT) ditambah dengan penerapannya yang

tidak hanya pada komputer atau perangkat jaringan pada umumnya. Begitu mudahnya

sekarang ini dalam menemukan source code atau binary resource untuk berbagai

macam protokol pendukung IoT yang disediakan untuk para hobby dan developer,

salah satunya protokol Message Queiuing Telemetry Transport (MQTT). MQTT menjadi salah satu protokol yang banyak digunakan pada aplikasi IoT karena

memiliki ukuran paket data yang kecil sehingga cocok digunakan pada aplikasi real-

time atau aplikasi yang membutuhkan kemampuan data streaming yang baik. Dari

beberapa info yang penulis dapatkan dari dosen dan referensi di internet, protokol

MQTT sudah beberapa kali dijadikan bahan pembahasan untuk keperluan tugas akhir

atau skripsi, namun masih memanfaatkan cloud MQTT broker yang sudah siap pakai.

Dalam penerapannya cloud MQTT broker harus menggunakan koneksi internet

walaupun hanya untuk perangkat yang letaknya tidak jauh atau berdekatan. Tentu

akan menghambat komunikasi antar client dengan cloud broker bila saat koneksi

internet atau Internet Service Provider (ISP) yang sering mengalami gangguan

terutama instansi yang berada di daerah tepencil atau masih belum dijangkau banyak

ISP lain yang handal. Sehingga untuk mengatasinya agar lebih efisien perlu adanya

penerapan MQTT yang cukup memanfaatkan jaringan lokal yang sudah tersedia di

suatu instansi tanpa harus memakan bandwidth internet.

Salah satu penyedia open-source MQTT client & broker yaitu Eclipse Mosquitto.

Dengan menggunakan Mosquitto kita dapat menerapkan protokol MQTT pada

jaringan lokal. Mosquitto juga menyediakan binary yang mendukung berbagai

macam sistem operasi seperti Windows, Linux, dan Mac. Bahkan Mosquitto juga

dapat dipasang pada single board computer (SBC) seperti Raspberry Pi. Dengan

memanfaatkan low power single board computer sebagai MQTT broker maka kita

tidak perlu menggunakan sebuah Personal Computer (PC) yang harus standby selama

koneksi dengan broker diperlukan terkait pertimbangan penggunaan daya. Selain itu

output data dari client juga dapat ditampilkan pada sebuah database dengan

merancang GUI pada SBC tersebut. Salah satu platform GUI yang dapat digunakan,

yaitu Qt yang juga menyediakan tools designer untuk mempermudah developer saat

merancang GUI dengan fitur konversi hasil desain ke bahasa pemrograman seperti

C/C++ ataupun Python (PyQt). Maka dari pemaparan di atas penulis akan membuat

sebuah skripsi dengan judul “Penerapan Mosquitto Sebagai Server MQTT Lokal

pada Komunikasi Antara Database MongoDB dan Mesin Absensi Multi-node”.

### 1.2 Perumusan Masalah

Berdasarkan uraian latar belakang, maka dapat dirumuskan masalah yang akan

dibahas:

1. Cara menerapkan MQTT pada mesin absensi menggunakan jaringan lokal.
2. Proses implementasi library Mosquitto pada Single Board Computer (SBC)

dalam hal ini Raspberry Pi.

3. Perancangan algoritma komunikasi antara beberapa Node atau Client (mesin

absensi) dengan Broker MQTT sekaligus mengakses database.

### 1.3 Tujuan

Adapun tujuan dari perancangan yang akan dilakukan adalah sebagai berikut:

1. Menerapkan protokol MQTT pada mesin absensi di local area network

dengan mengandalkan access point terdekat untuk komunikasi lebih handal

dan aman.

2. Menginstalasi Mosquitto pada Single Board Computer (SBC) salah satunya

Raspberry Pi.

3. Menerapkan algoritma komunikasi bidirectional dari protokol MQTT pada

perangkat-perangkat yang terhubung pada jaringan lokal atau jaringan publik.

4. Menggunakan aplikasi GUI designer PyQt5 dan penerapannya untuk

menginput, mengedit, dan menampilkan data dari suatu database dengan

konsep NoSQL salah satunya MongoDB dengan library Pymongo pada

Python.

### 1.4 Luaran

Beberapa manfaat yang dapat diperoleh dari perancangan di bawah ini adalah:

1. Diterapkannya teknologi mesin absensi secara wireless dengan memanfaatkan

jaringan lokal untuk logging kehadiran karyawan pada umumnya bagi instansi

dengan area yang luas dan yang sering mengalami gangguan koneksi ke ISP.

2. Sebagai referensi baru mengenai penerapan open-source MQTT broker untuk

modul pembelajaran dan praktikum (jobsheet).

3. Publikasi untuk proyek Small and Cheap Attendance Node (SCAN) yang

open-source dalam forum komunitas elektronika, mikrokontroler, dan otomasi

sehingga dapat dipelejari, diterapkan, dan dikembangkan secara umum.

II. TINJAUAN PUSTAKA

### 2.1 Protokol MQTT

Protokol MQTT menggunakan konsep publish/subscribe yang sangat berbeda

dengan konsep protokol yang lain seperti HTTP yang menggunakan paradigma

request/response. Titik pusat komunikasi adalah MQTT broker yang bertanggung

jawab untuk mengirim semua pesan di antara pengirim dan penerima yang sah. [2]

Setiap client yang mengirim pesan ke broker harus menyisipkan informasi nama

topik yang dituju. Topik adalah informasi routing untuk broker yang bertugas

mengarahkan pesan yang masuk kedalam broker. Client yang ingin menerima pesan

harus melakukan subscribe ke topik yang dituju dan selanjutnya broker akan

mengirimkan semua pesan yang diarahkan pada topik tersebut. Oleh karena itu client

tidak perlu saling mengenal, mereka dapat berkomunikasi melalui topik ini. [2]

Perbedaan mendasar dengan protokol HTTP adalah client tidak perlu menarik

informasi yang dibutuhkannya, melainkan broker akan mengirimkan informasi ke

client jika ada pesan baru yang masuk ke sebuah topik. Jika koneksi mengalami

gangguan maka MQTT broker dapat menyimpan semua pesan yang masuk dan

mengirimkannya kembali ke client ketika koneksi kembali normal. [2]

MQTT Client dapat bertindak sebagai publisher ataupun subscriber. MQTT

Client dapat berupa peralatan mikrokontroler maupun aplikasi komputer yang

ditanamkan library untuk dapat melakukan koneksi ke MQTT broker. Hardware bisa

sangat simpel (constrained device) yang terhubung secara wireless menggunakan

WiFi, maupun kabel ethernet. Implementasi Protokol MQTT pada client sangatlah

mudah, hal ini merupakan salah satu alasan mengapa MQTT ideal dan cocok untuk

small devices. Library MQTT client tersedia untuk banyak bahasa pemrograman

seperti Android, Arduino, C, C++, C#, Go, iOS, Java, JavaScript, .NET. MQTT client

dapat berupa objek yang mengirim dan menerima data. Tipe MQTT client tergantung fungsi kerjanya apakah sebagai publisher ataukah subscriber. MQTT Broker adalah

central device yang berfungsi untuk memproses komunikasi antara MQTT client dan

mendistribusikan pesan dari mereka pada topik-topik yang dituju. MQTT broker

dapat menangani ribuan devices dalam satu waktu. [2]

Arsitektur MQTT terdiri dari tiga komponen yaitu publisher, broker, dan

subscriber. Device yang menginginkan untuk terhubung pada suatu topik harus

diregistrasikan pada topik tersebut sebagai subscriber sehingga ketika publisher

mempublish informasi pada topik tersebut broker akan meneruskan informasi ke

subscriber. Otorisasi subscriber dan publisher dicek oleh broker untuk memastikan

keamanan terjaga sehingga bisa dipastikan bahwa publisher dan subscriber telah

diregristasikan pada broker. [2]

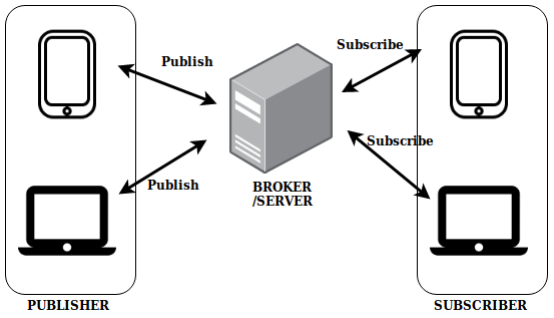
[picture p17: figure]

Gambar 2. 1 Arsitektur MQTT
(Sumber: Dasar Implementasi Protokol MQTT Menggunakan Python dan NodeMCU, 2019)

### 2.2 Mosquitto

Mosquitto menyediakan server yang sesuai standar dan implementasi client dari

protokol MQTT. MQTT menggunakan model publish/subscribe, memiliki overhead

jaringan yang rendah dan dapat diimplementasikan pada perangkat berdaya rendah

seperti mikrokontroler yang mungkin digunakan secara remote pada sensor Internet

of Things. Dengan demikian, Mosquitto dimaksudkan untuk digunakan dalam semua

situasi di mana ada kebutuhan untuk pengiriman pesan yang ringan, terutama pada

perangkat dengan resource terbatas. [6]

Proyek Mosquitto merupakan bagian dari Eclipse Foundation. Ada 3 bagian pada

proyek:

- Server utama Mosquitto
- mosquitto_pub dan mosquitto_sub client utilities yang merupakan salah

satu metode untuk berkomunikasi dengan server MQTT.

- Library MQTT client yang ditulis dalam C/C++ wrapper.

Mosquitto memungkinkan penelitian yang terkait langsung dengan protokol

MQTT itu sendiri, seperti membandingkan kinerja MQTT dan Constrained

Application Protocol (CoAP) [11] atau menyelidiki penggunaan OAuth di MQTT

[4]. Mosquitto mendukung kegiatan penelitian lainnya sebagai blok yang berguna

untuk membangun sistem berskala besar dan telah digunakan untuk mengevaluasi

MQTT untuk digunakan dalam Smart City Services [1] dan dalam pengembangan

sistem pemantauan lingkungan [3]. Mosquitto juga telah digunakan untuk

mendukung penelitian yang langsung digunakan sebagai bagian dari skema untuk

remote control dari suatu eksperimen [9].

Di luar akademisi, Mosquitto digunakan dalam proyek open-source lainnya

seperti proyek otomasi openHAB dan OwnTracks, proyek pelacakan lokasi pribadi,

dan telah terintegrasi ke dalam produk komersial. [6]

### 2.3 MQTT pada VLAN

Komunikasi MQTT pada Wide Area Network (WAN) dapat dibagi menjadi

jaringan yang lebih kecil menggunakan VLAN. Overhead pada DNS dari jaringan

lain tidak berpengaruh ke jaringan yang lebih kecil. Sehingga delay dan antrian yang

terjadi dapat dikurangi. [8]

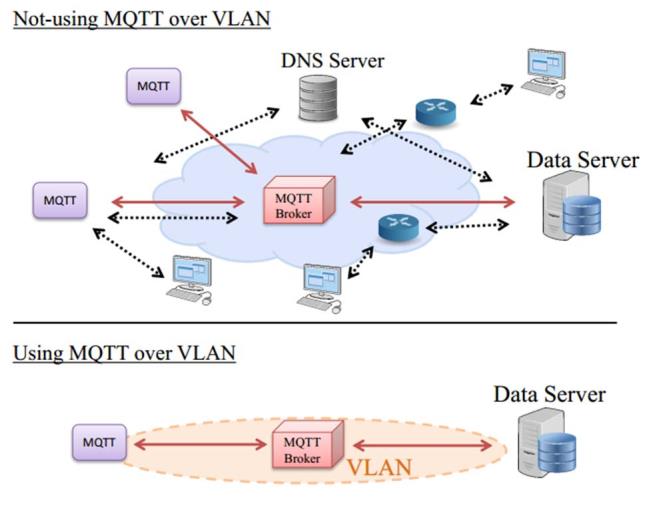
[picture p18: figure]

Gambar 2. 2 Arsitektur Jaringan MQTT dengan DNS Server dan VLAN

(Sumber: Sasaki. MQTT over VLAN for Reduction of Overhead on Information Discovery, 2019)

### 2.4 Attendance Based IoT and RFID System

RFID dan sistem IoT banyak diterapkan di berbagai bidang yang memerlukan

proses identifikasi seperti transportasi, medikal, perusahaan, dan keamanan. Tracking

kendaraan dan juga autentikasi pintu dikarenakan bersifat low cost device [10].

Dengan IoT sistem absensi dapat diterapkan secara cloud sehingga dapat menjadi

fleksibel dan dapat diakses di manapun selama ada koneksi ke internet. Prinsipnya

dengan membandingkan UID yang terbaca dengan UID yang ada pada database lalu

meng-update ke database tersebut. Selain itu RFID juga dapat dikombinasikan

dengan metode Capture Image menggunakan kamera.

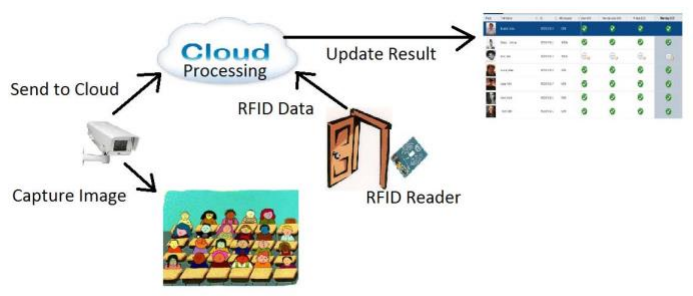
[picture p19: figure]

Gambar 2. 3 Arsitektur Attendance based RFID, Image, & cloud

(Sumber: Sharma. An automatic attendance monitoring system using RFID and IOT using Cloud, 2016)

### 2.5 MongoDB

Database NoSQL adalah database yang tidak menggunakan relasi antar tabel dan

tidak menyimpan data dalam format tabel baku seperti layaknya Relational Database

seperti SQL atau Oracle, PostgreSQL, MySQL dan SQL server [5].

Kelebihannya NoSQL tidak mengenal skema tabel yang kaku dengan format data

yang kaku. NoSQL cocok untuk data yang tidak terstruktur, istilah singkat untuk fitur

ini adalah Dynamic Schema. NoSQL juga menggunakan OOP dalam pengaksesan

atau manipulasi datanya. NoSQL bisa menampung data yang terstruktur, semi

terstruktur dan tidak terstuktur secara efesien dalam skala besar. [5]

MongoDB merupakan database open-source berbasis dokumen (Document-

Oriented Database) yang awalnya dibuat dengan bahasa C++. MongoDB sendiri

sudah dikembangkan oleh 10gen sejak Oktober 2007, namun baru dipublikasikan

pada Februari 2009. Selain karena performanya 4 kali lebih cepat dibandingkan

MySQL serta mudah diaplikasikan, karena telah tergabung juga sebagai modul PHP.

[5]

Kelebihannya adalah performa yang ditawarkan MongoDB lebih cepat

dibandingkan MySQL ini disebabkan oleh mem-cached dan format dokumennya

yang berbentuk seperti JSON, dan masih banyak lagi kelebihan lainnya. MongoDB

tersedia untuk platform Linux, Windows dan Mac. [5]

### 2.6 PyQt

PyQt menyatukan framework cross-platform Qt C++ dan Python cross-platform

interpreted. Qt lebih dari sekadar toolkit GUI. Ini termasuk abstraksi soket jaringan,

utas, Unicode, ekspresi reguler, basis data SQL, SVG, OpenGL, XML, peramban

web yang berfungsi penuh, sistem bantuan, kerangka multimedia, serta koleksi kaya

widget GUI. [7]

Kelas-kelas Qt menggunakan mekanisme sinyal/slot untuk berkomunikasi antara

objek-objek yang bertipe aman tetapi longgar digabungkan sehingga mudah untuk

membuat komponen perangkat lunak yang dapat digunakan kembali [7].

Qt juga mencakup Qt Designer, perancang GUI. PyQt dapat menghasilkan kode

Python dari Qt Designer. Dimungkinkan juga untuk menambahkan kontrol GUI baru

yang ditulis dengan Python ke Qt Designer. [7]

Python adalah bahasa berorientasi objek yang sederhana namun kuat.

Kesederhanaannya membuatnya mudah dipelajari, tetapi kekuatannya berarti aplikasi

besar dan kompleks dapat dibuat. Sifatnya yang ditafsirkan berarti bahwa

programmer Python sangat produktif karena tidak ada siklus pengembangan

kompilasi. [7]

Sebagian besar kekuatan Python berasal dari rangkaian modul ekstensi yang

komprehensif yang menyediakan berbagai fungsi termasuk server HTTP, parser

XML, akses basis data, alat kompresi data dan, tentu saja, antarmuka pengguna

grafis. Modul ekstensi biasanya diimplementasikan dalam Python, C atau C ++.

Menggunakan alat-alat seperti SIP membuat modul ekstensi yang merangkum library

C atau C ++ yang ada. Dengan cara ini, Python kemudian dapat menjadi lem untuk

membuat aplikasi baru dari library yang sudah ada. [7]

PyQt menggabungkan semua keunggulan Qt dan Python. Seorang programmer

memiliki semua kekuatan Qt, tetapi mampu mengeksploitasinya dengan

kesederhanaan Python. [7]

III. METODOLOGI DAN BENTUK TUGAS AKHIR

### 3.1 Perancangan Hardware

### 3.1.1 Blok Diagram Hardware

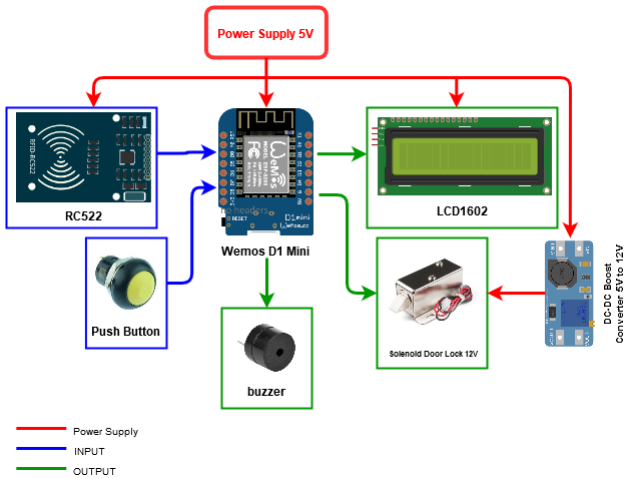
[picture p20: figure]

Gambar 3. 1 Blok Diagram Hardware Node Absensi

Pada hardware terdapat push button yang berfungsi untuk mengubah mode

apakah ingin membuka pintu atau melakukan absensi. Untuk fitur tambahan yaitu

pengunci pintu menggunakan solenoid dengan tegangan kerja 12 volt yang didapat

dari modul DC-DC boost converter untuk menaikkan tegangan dari 5 volt menjadi 12

volt.

### 3.1.2 Skema dan Tata Letak Rangkaian

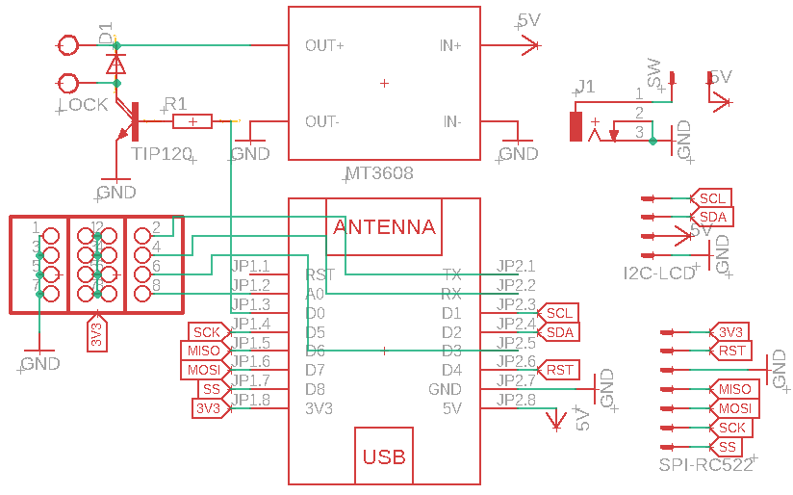
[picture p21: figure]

Gambar 3. 2 Skema Rangkaian Node Absensi

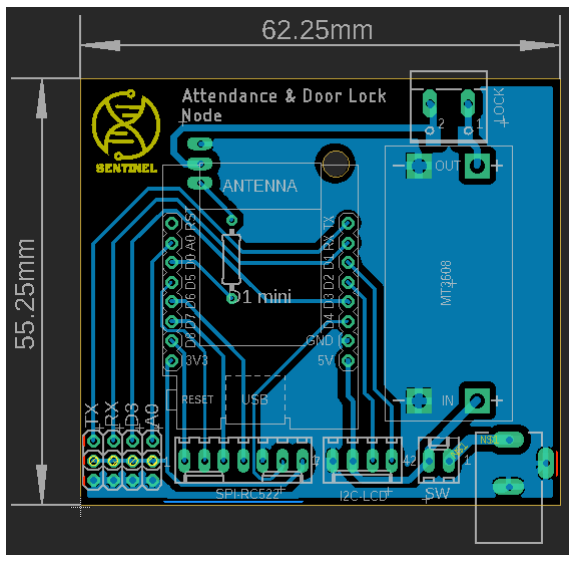
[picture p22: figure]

Gambar 3. 3 Tata Letak Rangkaian Node Absensi

### 3.2 Konfigurasi Jaringan

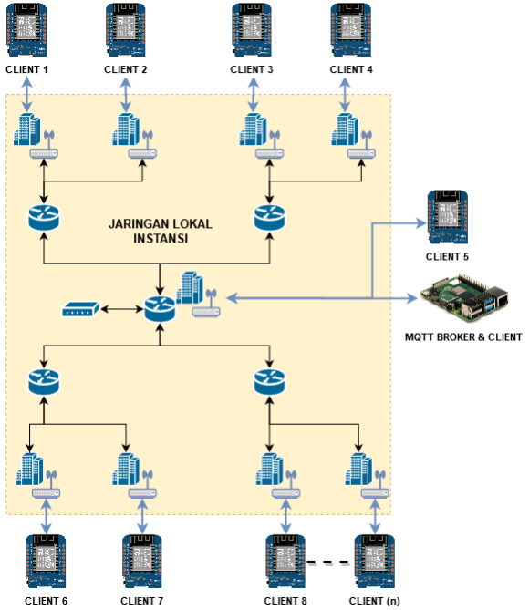
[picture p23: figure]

Gambar 3. 4 Konfigurasi jaringan sistem absensi

Pada Gambar 3.4 Raspberry Pi berfungsi sebagai MQTT broker atau server dan

sekaligus sebagai client yang sudah terinstall library MOSQUITTO. Untuk masing-

masing node absensi menggunakan Wemos D1 Mini sebagai MQTT client. Perangkat broker maupun client akan dihubungkan ke access point terdekat. Setiap client dapat

berada pada posisi yang jauh tergantung di mana karyawan akan melakukan absensi.

Yang terpenting semuanya terkoneksi ke 1 jaringan yang sama. Untuk penelitian ini

hanya digunakan 2 node absensi.

### 3.3 Perancangan Software dan Algoritma

### 3.3.1 Blok Diagram Algoritma

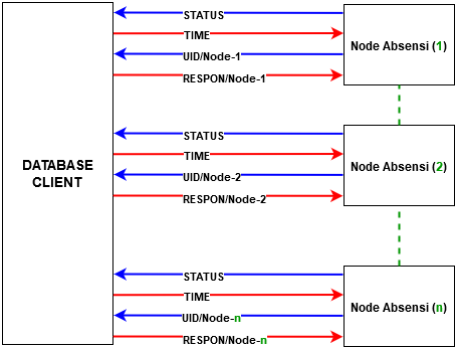
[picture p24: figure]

Gambar 3. 5 Blok Diagram Algoritma

Dari blok diagram 3.4 dapat dilihat bahwa tanda panah biru merupakan topik

yang di-subscribe oleh database client atau di-publish oleh node absensi. Sedangkan

tanda panah merah merupakan topik yang di-publish oleh database client atau di-

publish oleh node absensi.

Client terdiri dari database berupa komputer yang akan digunakan untuk

menyimpan dan mengolah database karyawan dan beberapa node absensi di banyak

titik. (n) merepresentasikan ID node yang akan digunakan sebagai client ID dalam protokol MQTT di setiap node. Pada database client juga terdapat GUI untuk

mempermudah administrator mengecek status koneksi masing-masing node,

menambahkan data karyawan baru, dan menghapus data dalam database.

Masing-masing node absensi akan mem-publish status koneksi ke database

client dengan periode waktu tertentu pada topik “STATUS”. Setiap node absensi

menggunakan fitur MQTT, yaitu “Last Will Message” jika suatu waktu koneksi

terputus. Message ini akan disimpan oleh broker dan akan diteruskan ke subscriber

topik “STATUS” jika salah satu publisher dalam hal ini setiap node absensi tiba-tiba

terputus koneksi dengan broker.

Bila node absensi mendeteksi kartu RFID seorang karyawan, UID dari kartu

akan di-publish melalui topik “UID/Node-n”. UID tersebut akan dicek oleh database

client apakah UID tersebut terdaftar dalam database atau tidak. Respon akan di-

publish oleh databse client ke topik “RESPON/Node-n”.

### 3.3.2 Flowchart Sistem Absensi

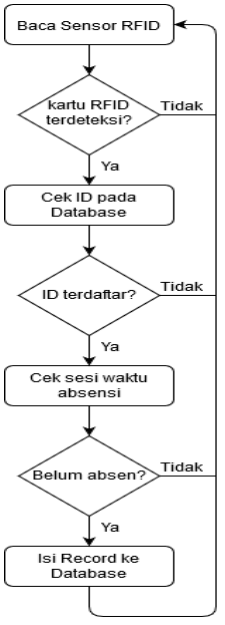
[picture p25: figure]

Gambar 3. 6 Flowchart Sistem Absensi

Cara kerja sistem digambarkan pada Gambar 3.5. Node absensi akan mengirim

setiap UID yang terbaca untuk selanjutnya dicek oleh server apakah UID terdaftar

atau tidak. Selanjutnya server akan memverifikasi apakah UID yang terdaftar sudah

melakukan absensi berdasarkan sesi waktu absensi saat ini. Database akan di-update

bila setelah dilakukan verifikasi karyawan belum melakukan absensi. Node absensi

akan menampilkan pesan ke LCD setelah menerima respon dari server. Setiap

aktivitas yang terjadi pada node absensi akan dikirim dan disimpan di log file pada

server.

IV. JADWAL PELAKSANAAN

No. | Kegiatan | Waktu Pelaksanaan (Bulan ke-)
1 | 2 | 3 | 4 | 5
1 | Perancangan proposal dan konsep sistem/alat yang akan dibuat
2 | Persiapan komponen dan perancangan, dan pembuatan hardware
3 | Pembuatan GUI, integrasi database dan algoritma
4 | Pengujian hardware dan software
5 | Analisis, perekapan, dan pelaporan hasil pengujian
V. ANGGARAN BIAYA
No. | Nama Komponen | Pemakaian Justifikasi | Jumlah | Harga | Harga Keseluruhan
1 | Modul Raspberry Pi 3B (second) | Sebagai broker dan database | 1 | Rp 400,000 | Rp 400,000
2 | MicroSD Sandisk Ultra A1 16GB | Drive penyimpanan pada Raspberry Pi | 1 | Rp 58,000 | Rp 58,000
3 | Wemos D1 Mini | Kontroler masing-masing node (mesin absensi) | 2 | Rp 35,000 | Rp 70,000
4 | Modul MFRC522 | Scanner kartu RFID | 2 | Rp 20,000 | Rp 40,000
5 | Modul LCD1602 + I2C adaptor | Display untuk masing-masing node | 2 | Rp 25,000 | Rp 50,000
6 | Adaptor 5V 3A | Catu daya untuk modul Wemos dan Raspberry Pi | 3 | Rp 30,000 | Rp 90,000

7

Boost
Converter
MT3608 2A

Untuk output
tegangan ke
solenoid di setiap
node (opsional)
2 | Rp | 7,000 | Rp | 14,000
8 | PCB (cutting, masking, & overlay) | Board sistem minimum setiap node | 2 | Rp 55,000 | Rp 110,000
9 | komponen lain | komponen elektronika pendukung lainnya | 1 | Rp 75,000 | Rp 75,000
10 | Cutting Acrylic | Casing penutup untuk setiap node | 2 | Rp 100,000 | Rp 200,000
11 | Monitor bekas | Untuk Rapsberry Pi3 | 1 | Rp 400,000 | Rp 400,000
Total Biaya | | | | | Rp 1,507,000

DAFTAR PUSTAKA

[1]Antonić, A., M. Marjanović, P. Skočir, and I. P. Žarko. (2015). Comparison of the CUPUS Middleware and MQTT Protocol for Smart City Services. In 2015 13th
International | Conference | on | Telecommunications | (ConTEL), | 1–8.
doi:10.1109/ConTEL.2015.7231225.

[2]Atmoko, Rachmad Andri. (2019). Dasar Implementasi Protokol MQTT Menggunakan Python dan NodeMCU. Blitar: Mokosoft Media.

[3]Bellavista, Paolo, Carlo Giannelli, and Riccardo Zamagna. (2017). The Pervasive Environment Sensing and Sharing Solution. Sustainability 9 (4): 585. doi:10.3390/su9040585.

[4]Fremantle, P., B. Aziz, J. Kopecký, and P. Scott. (2014). Federated Identity and Access Management for the Internet of Things. In 2014 International Workshop on Secure Internet of Things, 10–17. doi:10.1109/SIoT.2014.8.

[5]IdCloudHost. (2017, Juli 7). Mengenal Lebih Dekat Tentang Database MongoDB. Januari 23, 2019.
https://idcloudhost.com/mengenal-lebih-dekat-tentang-database-mongodb/

[6]Light, R.A. (2017). Mosquitto: server and client implementation of the MQTT
protocol. | Journal | of | Open | Source | Software, | 2(13), | 265,
doi:10.21105/joss.00265.

[7]Riverbank Computing Limited. What is Pyqt?. Januari 23, 2019. https://www.riverbankcomputing.com/software/pyqt/intro

[8]Sasaki, Y., Yokotani, T., & Mukai, H. (2019). MQTT over VLAN for Reduction of Overhead on Information Discovery. 2019 International Conference on Information Networking (ICOIN). doi:10.1109/icoin.2019.8718125.

[9]Schulz, M., F. Chen, and L. Payne. (2014). Real-Time Animation of Equipment in a Remote Laboratory. In 2014 11th International Conference on Remote
Engineering | and | Virtual | Instrumentation | (REV), | 172–76.
doi:10.1109/REV.2014.6784247.

[10]Sharma, T., & Aarthy, S. L. (2016). An automatic attendance monitoring system using RFID and IOT using Cloud. 2016 Online International Conference on
Green | Engineering | and | Technologies | (IC-GET).
doi:10.1109/get.2016.7916851.

[11]Thangavel, D., X. Ma, A. Valera, H. X. Tan, and C. K. Y. Tan. (2014). Performance Evaluation of MQTT and CoAP via a Common Middleware. In 2014 IEEE Ninth International Conference on Intelligent Sensors, Sensor
Networks | and | Information | Processing | (ISSNIP), | 1–6.
doi:10.1109/ISSNIP.2014.6827678.

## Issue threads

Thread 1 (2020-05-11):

Multitasking GUI

khyarul, 2020-05-11:
Aplikasi GUI Python S.C.A.N Node monitor akan menghandle dan berkomunikasi dengan banyak Node yg terdaftar pada "Node List" Database. Spesifikasinya:

1. Otomatis membuat Thread setelah klik button "Connect".
2. Jumlah Thread yang dibuat tergantung jumlah Node yang ada. **N(thread) = N(node)**
3. Masing-masing thread menghandle banyak Topic dengan format: "namaTopic/**Node_n**", di mana **Node_n** merupakan Client ID setiap Node yang unik.
4. Module multitasking bisa menggunakan: **concurrent.futures** atau **threading** di Python 3.7

khyarul, 2020-05-11:
`"""Programmed by Khyarul Arham"""
########GUI Module#######
from subprocess import Popen
import sys, os
from PyQt5.QtWidgets import *
from PyQt5.QtCore import *
from PyQt5.QtGui import *
from PIL import Image
########Database Module#########
from pymongo import MongoClient
########MQTT Module#############
import paho.mqtt.client as mqttClient
################################
import threading
import time

#################Inisiasi Database#######################
dbClient = MongoClient("mongodb://localhost:27017/")
db = dbClient['ATTENDANCE']
collection = db['NODE']

#################MQTT Callback Event###########################
def on_connect(client, userdata, flags, rc):
    print('Code', str(rc), end=' ')
    if rc == 0:
        # Client.subscribe('UID/Node_' + NODE)
        # Client.subscribe('STATUS/Node_' + NODE, 2)
        print('Connection successful')
    elif rc == 1:
        print('Connection refused - incorrect protocol version')
    elif rc == 2:
        print('Connection refused - invalid client identifier')
    elif rc == 3:
        print('Connection refused - server unavailable')
    elif rc == 4:
        print('Connection refused - bad username or password')
    elif rc == 5:
        print('Connection refused - not authorised')

def on_message(client, userdata, message):
    message.payload = message.payload.decode('utf-8')
    topic = message.topic

###############MQTT global variable####################
client = None
Client = ''
Username = ''
Password = ''
Host = ''
Port = None

#################Inisiasi MQTT###########################

#################Main Window########################
class MainWindow(QWidget):
    def __init__(self):
        super().__init__()
        self.setWindowTitle('S.C.A.N - Node Monitor')
        self.setWindowIcon(QIcon('icons/node.png'))
        self.resize(1000, 300)
        self.setup()
        # self.showMaximized()
        self.show()

    def setup(self):
        self.widget()
        self.layouts()
        self.getNode()

    def widget(self):
        font = QFont()
        font.setPointSize(10)
        font1 = QFont()
        font1.setPointSize(11)
        font1.setBold(True)
        self.serverConfigLabel = QLabel('MQTT Server Configuration')
        self.serverConfigLabel.setFont(font1)
        self.clientIDInput = QLineEdit()
        self.clientIDInput.setText('NODE MONITOR')
        self.clientIDInput.setPlaceholderText('Client ID')
        self.hostInput = QLineEdit()
        self.hostInput.setPlaceholderText('IP/Hostname')
        self.portInput = QLineEdit()
        self.portInput.setText('1883')
        self.portInput.setPlaceholderText('Port (default: 1883)')
        self.usernameInput = QLineEdit()
        self.usernameInput.setPlaceholderText('Username')
        self.passInput = QLineEdit()
        self.passInput.setPlaceholderText('Password')
        self.passInput.setEchoMode(QLineEdit.Password)
        self.authCheck = QCheckBox('Use Authentication', self)
        self.toggleAuth()
        self.authCheck.toggled.connect(self.toggleAuth)
        self.connectBtn = QRadioButton('CONNECT')
        self.connectBtn.setStyleSheet('background-color: rgb(122,255,112);')
        self.connectBtn.setIcon(QIcon('icons/connect'))
        self.connectBtn.setFont(font)
        self.connectBtn.setFixedWidth(100)
        self.connectBtn.toggled.connect(self.connectMqtt)
        self.connectStatus = QLabel('DISCONNECTED')

        self.nodeInfoLabel = QLabel('Node Information')
        self.nodeInfoLabel.setFont(font1)
        self.nodeAlias = QLabel()
        self.nodeClient = QLabel()
        self.nodeStatus = QLabel()
        self.nodeDoorStatus = QLabel()
        self.unlockDoorBtn = QPushButton('Unlock Door')
        self.unlockDoorBtn.setIcon(QIcon('icons/unlock'))
        self.unlockDoorBtn.setFont(font)
        self.unlockDoorBtn.setFixedWidth(100)

        self.serverConfigFrame = QFrame()
        self.serverConfigFrame.setStyleSheet('background-color: white;')
        self.serverConfigFrame.setFrameShape(QFrame.Panel)
        self.serverConfigFrame.setFrameShadow(QFrame.Raised)
        self.nodeInfoFrame = QFrame()
        self.nodeInfoFrame.setStyleSheet('background-color: white;')
        self.nodeInfoFrame.setFrameShape(QFrame.Panel)
        self.nodeInfoFrame.setFrameShadow(QFrame.Raised)
        self.logLabel = QLabel('Event Log')
        self.logLabel.setFont(font1)
        self.logList = QListWidget()

        self.nodeLabel = QLabel('Node List')
        self.nodeLabel.setFont(font1)
        self.pingBtn = QPushButton('PING')
        self.pingBtn.setIcon(QIcon('icons/ping.png'))
        self.pingBtn.setFont(font)
        self.pingBtn.clicked.connect(self.getNode)
        self.nodeList = QListWidget()
        self.nodeList.itemSelectionChanged.connect(self.showNode)
        self.addBtn = QPushButton('Add')
        self.addBtn.setIcon(QIcon('icons/add.png'))
        self.addBtn.setFont(font)
        self.addBtn.clicked.connect(self.addNode)
        self.editBtn = QPushButton('Edit')
        self.editBtn.setIcon(QIcon('icons/edit.png'))
        self.editBtn.setFont(font)
        self.editBtn.clicked.connect(self.editNode)
        self.deleteBtn = QPushButton('Remove')
        self.deleteBtn.setIcon(QIcon('icons/remove.png'))
        self.deleteBtn.setFont(font)
        self.deleteBtn.clicked.connect(self.deleteNode)
        self.employeeBtn = QPushButton('Employee Manager')
        self.employeeBtn.setIcon(QIcon('icons/person.png'))
        self.employeeBtn.setFont(font)
        self.employeeBtn.clicked.connect(self.openEmployee)

    def layouts(self):
        self.mainLayout = QHBoxLayout()
        self.leftLayout = QVBoxLayout()
        self.leftTopLayout = QHBoxLayout()
        self.leftTopLayout1 = QVBoxLayout()
        self.connectLayout = QHBoxLayout()
        self.leftTopLayout2 = QVBoxLayout()
        self.unlockDoorLayout = QHBoxLayout()
        self.leftBotLayout = QVBoxLayout()
        self.rightLayout = QVBoxLayout()
        self.rightTopLayout = QHBoxLayout()
        self.rightBotLayout = QHBoxLayout()
        self.serverInfo = QGridLayout(self.serverConfigFrame)
        self.serverInfo.setAlignment(Qt.AlignLeft)
        self.nodeInfo = QGridLayout(self.nodeInfoFrame)
        self.nodeInfo.setAlignment(Qt.AlignLeft)

        self.mainLayout.addLayout(self.leftLayout, 77)
        self.mainLayout.addLayout(self.rightLayout, 23)
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
khyarul, 2020-05-11:
`    def connectMqtt(self):
        global client
        Client = self.clientIDInput.text()
        Username = self.usernameInput.text()
        Password = self.passInput.text()
        Host = self.hostInput.text()
        Port = self.portInput.text()
        if self.connectBtn.isChecked():
            client = mqttClient.Client(Client)
            if self.authCheck.isChecked():
                client.username_pw_set(Username, Password)
            client.on_message = on_message
            client.on_connect = on_connect
            try:
                client.connect(Host, int(Port), 60)
                client.loop_start()
                self.connectStatus.setText('CONNECTED')
                for x in range(self.nodeList.count()):
                    data = self.nodeList.item(x).text()
                    clientID = data.split(' - ')[1]
                    self.connectThread = threading.Thread(target=self.connectThreadFunc, args=[clientID])
                    self.connectThread.start()
            except:
                print('Connection Failed')
                self.connectBtn.setChecked(False)
                self.connectStatus.setText('DISCONNECTED')
        else:
            client.disconnect()
            self.connectStatus.setText('DISCONNECTED')`

khyarul, 2020-05-11:
Test multithreading (baris kode dicetak tebal):

1. baca list Node dan split data untuk ambil ClientID
2. Jalankan methode: **connectThreadFunc** dengan argument **clientID** yg didapat dari list Node
3. Masing-masing thread berjalan (seolah) bersamaan dengan interval 1 detik

```
    def connectMqtt(self):
        global client
        Client = self.clientIDInput.text()
        Username = self.usernameInput.text()
        Password = self.passInput.text()
        Host = self.hostInput.text()
        Port = self.portInput.text()
        if self.connectBtn.isChecked():
            client = mqttClient.Client(Client)
            if self.authCheck.isChecked():
                client.username_pw_set(Username, Password)
            client.on_message = on_message
            client.on_connect = on_connect
            try:
                client.connect(Host, int(Port), 60)
                client.loop_start()
                self.connectStatus.setText('CONNECTED')
                **for x in range(self.nodeList.count()):
                    data = self.nodeList.item(x).text()
                    clientID = data.split(' - ')[1]
                    self.connectThread = threading.Thread(target=self.connectThreadFunc, args=[clientID])
                    self.connectThread.start()**
            except:
                print('Connection Failed')
                self.connectBtn.setChecked(False)
                self.connectStatus.setText('DISCONNECTED')
        else:
            client.disconnect()
            self.connectStatus.setText('DISCONNECTED')
```

```
**def connectThreadFunc(self, client):
        cnt = 0
        while True:
            if self.connectBtn.isChecked() == False:
                break
            print(client)
            cnt += 1
            time.sleep(1)**
```

khyarul, 2020-05-17:
update on [SCAN_node_monitor](https://github.com/khyarul/S.C.A.N/blob/master/GUI/SCAN_node_monitor.pyl) & [karyawan.py](https://github.com/khyarul/S.C.A.N/blob/master/GUI/karyawan.py)

Beberapa update:
- Thread pengiriman waktu ke semua Node setiap 5 detik
- Dynamic variable untuk meringkas baris program dalam menyimpan data setiap node dengan topic yang berbeda-beda
- Menampilkan CONNECTION STATUS setiap node.
- Fitur "Log Event" dikelompokkan berdasarkan tanggal dan diurutkan berdasarkan  waktu event.
- Fitur "Unlock Door" sudah berfungsi, membuka kunci solenoid masing-masing node.

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

khyarul, 2020-05-18:
update on [SCAN_node_monitor.py](https://github.com/khyarul/S.C.A.N/blob/master/GUI/SCAN_node_monitor.py), [karyawan.py](https://github.com/khyarul/S.C.A.N/blob/master/GUI/karyawan.py), & [S.C.A.N_OTA.ino](https://github.com/khyarul/S.C.A.N/blob/master/Arduino/S.C.A.N_OTA.ino)

**All features are working now! Release version 1.0**
🥇 🥇 🥇

Closed 2020-05-18.

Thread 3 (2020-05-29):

I/O Expander using PCF8574 and other fix for schematic

khyarul, 2020-05-29:
- I/O port for all button, buzzer, and magnet switch will use I2C expander PCF8574.
- Add transistor for driving the buzzer.
- change the output connector of solenoid and magnet switch for easy plug & play.

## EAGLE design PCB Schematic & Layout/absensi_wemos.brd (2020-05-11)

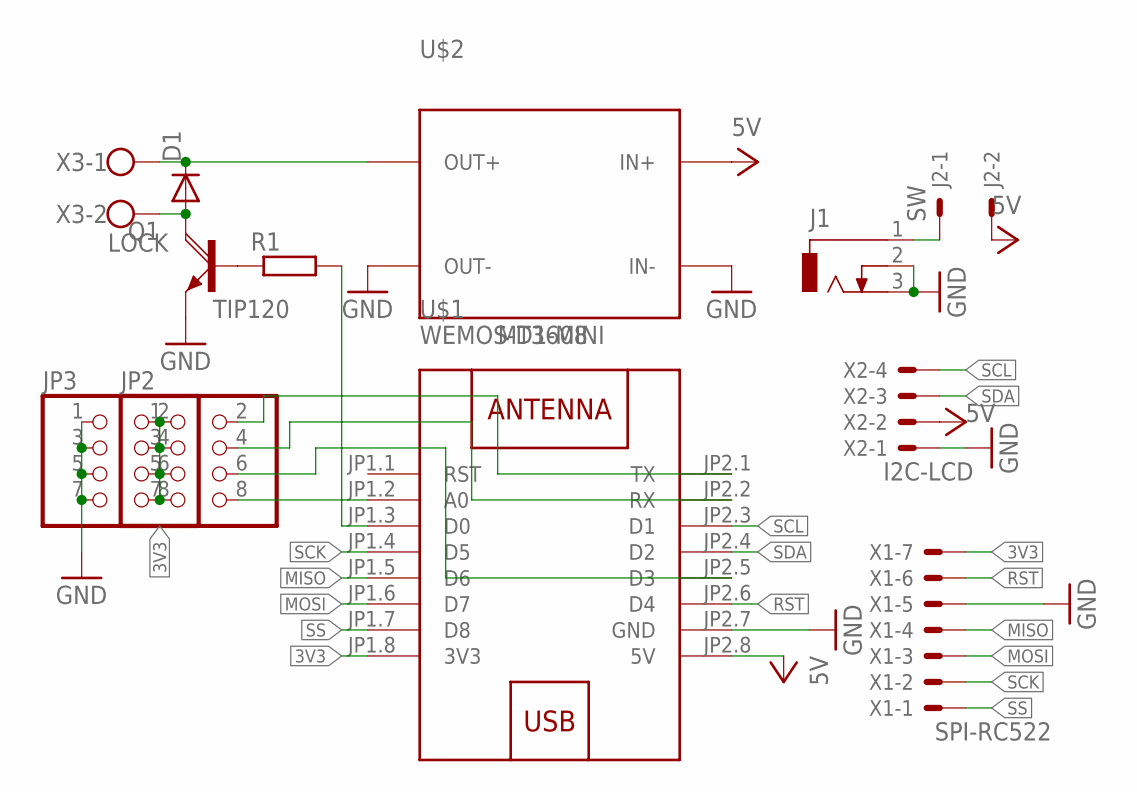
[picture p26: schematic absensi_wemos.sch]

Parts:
D1: DIODE-DO-214AC; DO-214AC
J1: DCJ0303
J2: SW; 6410-02
JP2, JP3: PINHD-2X4; 2X04
Q1: TIP120; TO220AH
R1: R0207/10; 0207/10
U$1: WEMOS-D1-MINI
U$2: MT3608; DC-DC-STEP-UP-MT3608
X1: SPI-RC522; 6410-07
X2: I2C-LCD; 6410-04
X3: LOCK; W237-102

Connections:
3V3: JP2.1, JP2.3, JP2.5, JP2.7, JP3.2, JP3.4, JP3.6, JP3.8, U$1.JP1.8 (3V3), X1.7
GND: J1.2, J1.3, JP3.1, JP3.3, JP3.5, JP3.7, Q1.E, U$1.JP2.7 (GND), U$2.IN-, U$2.OUT-, X1.5, X2.1
MISO: U$1.JP1.5 (D6), X1.4
MOSI: U$1.JP1.6 (D7), X1.3
unnamed: J1.1, J2.1
unnamed: R1.2, U$1.JP1.3 (D0)
unnamed: Q1.B, R1.1
unnamed: D1.C, U$2.OUT+, X3.1
unnamed: D1.A, Q1.C, X3.2
unnamed: JP2.8, U$1.JP1.2 (A0)
unnamed: JP2.6, U$1.JP2.5 (D3)
unnamed: JP2.4, U$1.JP2.2 (RX)
unnamed: JP2.2, U$1.JP2.1 (TX)
RST: U$1.JP2.6 (D4), X1.6
SCK: U$1.JP1.4 (D5), X1.2
SCL: U$1.JP2.3 (D1), X2.4
SDA: U$1.JP2.4 (D2), X2.3
SS: U$1.JP1.7 (D8), X1.1
VCC: J2.2, U$1.JP2.8 (5V), U$2.IN+, X2.2

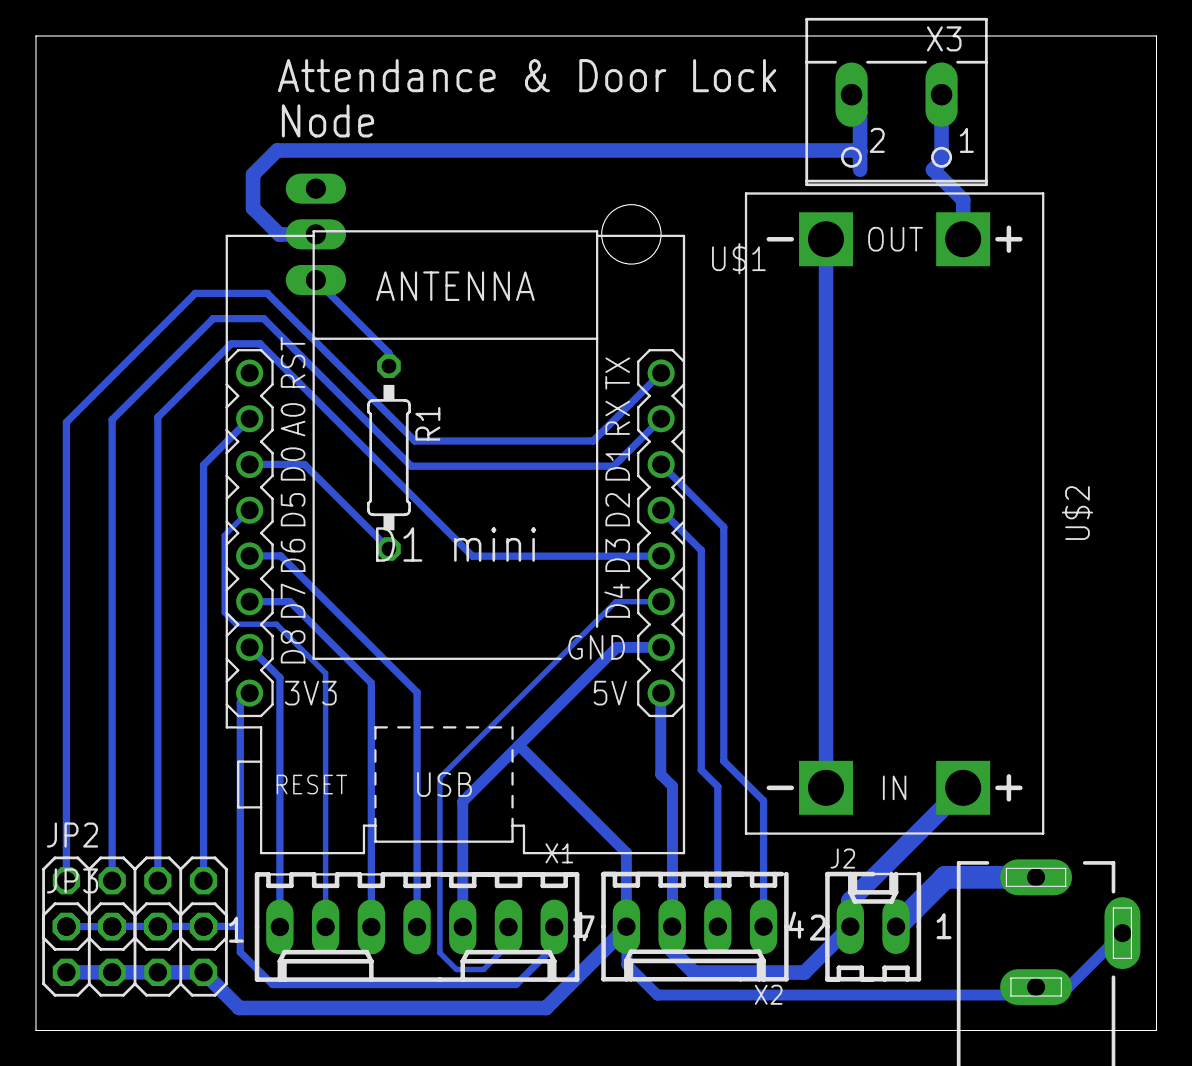
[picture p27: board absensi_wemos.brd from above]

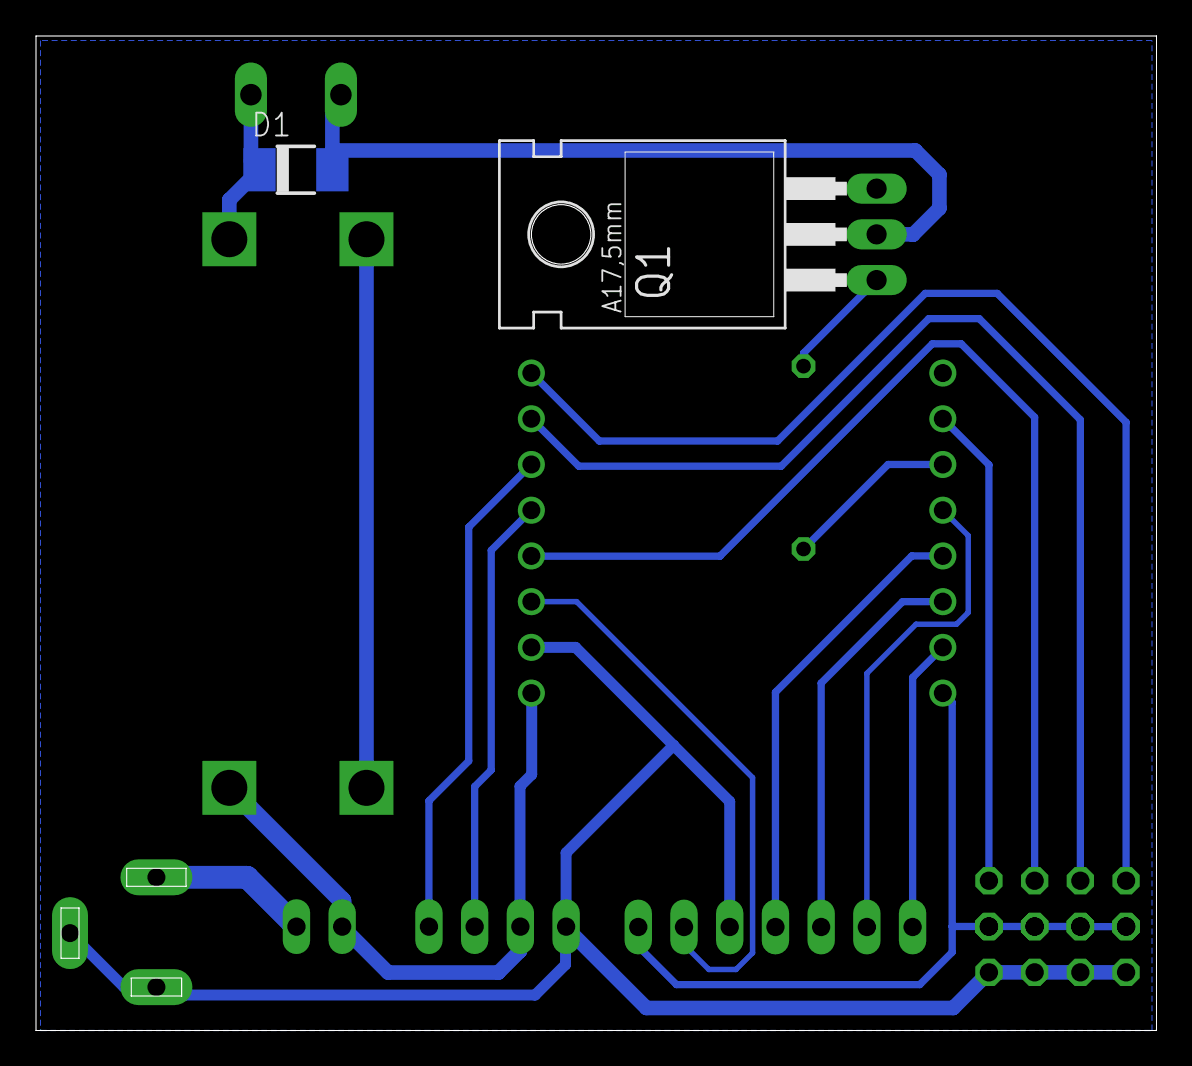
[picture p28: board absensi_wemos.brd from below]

Board: 2 copper layers, 62.2 x 55.2 mm, 12 parts (2 on the bottom side), 19 nets.

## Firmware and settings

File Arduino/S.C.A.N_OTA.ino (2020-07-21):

/*
   MQTT Small & Cheap Attendance Node (S.C.A.N) V1.0
   Programmed by Khyarul Arham - Sentinel
*/
#include <Scheduler.h>
#include <ESP8266WiFi.h>
#include <ESP8266mDNS.h>
#include <WiFiUdp.h>
#include <ArduinoOTA.h>
#include <PubSubClient.h>
#include <Wire.h>
#include <LiquidCrystal_I2C.h>
#include <SPI.h>
#include <MFRC522.h>

#define SS_PIN D8
#define RST_PIN D4

LiquidCrystal_I2C lcd(0x27, 16, 2);
MFRC522 rfid(SS_PIN, RST_PIN); // Instance of the class
MFRC522::MIFARE_Key key;

const char* ssid PROGMEM = "WiFi SSID"; //WiFi Host
const char* pass PROGMEM = "WiFi password";          //WiFi pass

const char* broker PROGMEM = "mqttserver.x";    //mqtt host
const int16_t port PROGMEM = 1883;              //mqtt port
const char* clientID PROGMEM = "Node_x";        //mqtt client ID, cukup ganti angka di belakangnya saja, "Node_" jangan diganti/dihapus
const int8_t auth PROGMEM = 1;                  //authentication require: use username & password (1 = yes, 0 = no)
const char* username PROGMEM = "SCAN_MONITOR";      //mqtt username
const char* password PROGMEM = "mqttpassword";    //mqtt pass

const char* host PROGMEM = "S.C.A.N-Node_x";    //OTA host name, bebas
const char* otaPass PROGMEM = "51eee58782ddfa75220078c574e15142"; //is "OTAPASSWORD" after hashed, OTA update MD5 hashed password, change with your own password with md5 hash

int8_t BUZZER = 0, preButton = 1, doorButton = 1, SCREEN = 1, MODE = 0;
uint8_t screenTimer = 10;   //Screen will turn OFF after x seconds idle (default 10s)
//for measuring response time from UID publish until receive again the response message from Monitor Client (the amount of time needed for authentication process)
uint32_t sendTime, receiveTime; //"sendTime" after publish UID, "receiveTime" after receive the response from Node Monitor

WiFiClient wemos;
PubSubClient mqtt;

#define lock_ON digitalWrite(D0, 0)
#define lock_OFF digitalWrite(D0, 1)
String RESPON = "", TIME = "-No Time Update-", LOCK = "1";
//char TOPIC[16] = "";
char responTopic[16] = "RESPON/";
char uidTopic[16] = "UID/";
char statusTopic[16] = "STATUS/";
char lockTopic[16] = "LOCK/";     //remote button topic
char doorTopic[16] = "DOOR/";
//=========================Scheduler================================
//==================================================================
class mainLoop : public Task {
  public:
    void loop() {
mulai:
      lcd.setCursor(0, 0); lcd.print(TIME);
      //      char reedBuff[16];
      //      sprintf(reedBuff, "%4d", reed);
      //      lcd.setCursor(0,0); lcd.print(reedBuff);
      if (preButton == 0) {
        SCREEN = 1;
        MODE = 1;
      }
      else if (doorButton == 0) {
        SCREEN = 1;
        MODE = 0;
      }
      if (MODE == 0) {
        lcd.setCursor(0, 1); lcd.print(F(" TAP TO UNLOCK "));
      }
      else {
        lcd.setCursor(0, 1); lcd.print(F("ATTENDANCE MODE"));
      }
      yield();
      // Reset the loop if no new card present on the sensor/reader. This saves the entire process when idle. And if present, select one.
      if (!rfid.PICC_IsNewCardPresent() || !rfid.PICC_ReadCardSerial()) {
        goto mulai;
      }

      SCREEN = 1;
      MFRC522::PICC_Type piccType = rfid.PICC_GetType(rfid.uid.sak);
      String idStr = "";
      char id[16] = "";
      for (uint8_t i = 0; i < rfid.uid.size; i++) {
        idStr += String(rfid.uid.uidByte[i], HEX);
      }
      idStr.toUpperCase();
      if (MODE == 0) {
        idStr = "0:" + idStr;
      }
      else {
        idStr = "1:" + idStr;
      }
      lcd.clear();
      lcd.setCursor(0, 0); lcd.print(F("Checking..."));
      //      lcd.setCursor(0, 0); lcd.print(rfid.PICC_GetTypeName(piccType));
      //      lcd.setCursor(0, 1); lcd.print(idStr);
      strcpy_P(id, idStr.c_str());
      mqtt.publish(uidTopic, id);
      sendTime = millis();  //start timer after publish

      char buff[6];
      while (1) {
        if (RESPON == "" && (millis() - sendTime >= 4000)) {         //Authentication timeout
          BUZZER = 2;
          lcd.clear();
          lcd.setCursor(0, 0); lcd.print(F("Sorry:( TIMEOUT"));
          lcd.setCursor(0, 1); lcd.print(F(" Pls TRY AGAIN "));
          break;
        }
        else if (RESPON == "0") {                               //Unregistered, RESPON from Monitor Client = 0
          sprintf(buff, "%d", receiveTime);
          BUZZER = 2;
          lcd.clear();
          lcd.setCursor(0, 0); lcd.print(F("    Sorry :(   "));
          lcd.setCursor(0, 1); lcd.print(F("UNREGISTERED ID"));
          mqtt.publish("PERIOD", buff);
          break;
        }
        else if (RESPON != "" && RESPON != "0") {
          sprintf(buff, "%d", receiveTime);
          BUZZER = 1;
          lcd.clear();
          if (MODE == 0) {
            LOCK = "0";
            lcd.setCursor(0, 0); lcd.print(RESPON);
            lcd.setCursor(0, 1); lcd.print(F("UNLOCK THE DOOR "));
          }
          else {
            lcd.setCursor(0, 0); lcd.print(RESPON);
            lcd.setCursor(0, 1); lcd.print(F("   PRESENT :)   "));
          }
          mqtt.publish("PERIOD", buff);
          break;
        }
        yield();
      }
      sendTime = 0;
      receiveTime = 0;
      RESPON = "";
      MODE = 0;
      rfid.PICC_HaltA();        // Halt PICC
      rfid.PCD_StopCrypto1();   // Stop encryption on PCD
      delay(2000);
      lcd.clear();
      //lcd.noBacklight();
    }
} main_loop;
//==================================================================
class mqttLoop : public Task {
  public:
    void loop() {
      if (!mqtt.connected()) {
        if (auth == 1) {
          mqtt.connect(clientID, username, password, statusTopic, 2, 0, "0");   //mqtt.connect(clientID, statusTopic, 2, 0, "0");
        }
        else {
          mqtt.connect(clientID, statusTopic, 2, 0, "0");
        }
        mqtt.publish(statusTopic, "1"); //1=CONNECT, 0=DISCONNECT
        mqtt.subscribe(responTopic);
        mqtt.subscribe("PING");
        mqtt.subscribe("TIME");
        mqtt.subscribe(lockTopic);
      }
      mqtt.loop();
      delay(10);
    }
} mqtt_loop;
//==================================================================
//======================Button and Door Sensor======================
class buttonLoop : public Task {
  public:
    uint16_t reed;
    bool door = 0, doorState = 0;
    void setup() {
      //read Door Sensor on startup
      readDoor();
      if (door == 0) {
        mqtt.publish(doorTopic, "0");
      }
      else {
        mqtt.publish(doorTopic, "1");
      }
    }
    //===========
    void loop() {
      preButton = digitalRead(TX);
      doorButton = digitalRead(D3);
      //Baca & kirim status pintu saat berubah dari kondisi sebelumnya
      readDoor();
      if (doorState != door) {
        char buff[2];
        sprintf(buff, "%d", door);
        mqtt.publish(doorTopic, buff);
        doorState = door;
      }
      delay(50);
    }
    //Baca Sensor Reed/Magnet
    void readDoor() {
      reed = analogRead(A0);
      if (reed < 512) {
        door = 0;
      }
      else {
        door = 1;
      }
    }
} button_loop;
//==================================================================
class solenoidLoop : public Task {
  public:
    void loop() {
      if (LOCK == "0") {  //kunci OFF, buka kunci, solenoid ON
        lock_OFF;
        BUZZER = 1;
        delay(5000);
        lock_ON;
        delay(200);
      }
      else {              //kunci ON, solenoid OFF
        lock_ON;
      }
      LOCK = "";
      delay(50);
    }
} solenoid_loop;
//==================================================================
class buzzerLoop : public Task {
  public:
    void loop() {
      if (BUZZER == 1) {
        digitalWrite(RX, 1);
        delay(100);
        digitalWrite(RX, 0);
        delay(100);
        digitalWrite(RX, 1);
        delay(100);
        digitalWrite(RX, 0);
        BUZZER = 0;
      }
      else if (BUZZER == 2) {
        digitalWrite(RX, 1);
        delay(700);
        digitalWrite(RX, 0);
        BUZZER = 0;
      }
      else {
        digitalWrite(RX, 0);
      }
      delay(50);
    }
} buzzer_loop;
//==================================================================
class otaLoop : public Task {
  public:
    void loop() {
      ArduinoOTA.handle();
      delay(20);
    }
} ota_loop;
//==================================================================
class screenLoop : public Task {
  public:
    void loop() {
      if (SCREEN == 1) {
        SCREEN = 0;
        lcd.backlight();
        uint32_t now = millis();
        while ((millis() - now) < (screenTimer * 1000)) {
          if (SCREEN == 1) {
            SCREEN = 0;
            lcd.backlight();
            now = millis();
          }
          delay(50);
        }
        lcd.noBacklight();
      }
      else {
        lcd.noBacklight();
      }
      delay(50);
    }
} screen_loop;
//==================================================================
//==================================================================

void setup() {
  pinMode(D0, OUTPUT);
  lock_ON;
  pinMode(D3, INPUT_PULLUP);
  pinMode(TX, INPUT_PULLUP);
  pinMode(RX, OUTPUT);

  lcd.begin();
  lcd.clear();
  lcd.setCursor(0, 0); lcd.print(" Connecting...  ");

  WiFi.mode(WIFI_STA);
  WiFi.begin(ssid, pass);
  while (WiFi.status() != WL_CONNECTED) {
    delay(100);
  }

  ArduinoOTA.setHostname(host);
  ArduinoOTA.setPasswordHash(otaPass);
  ArduinoOTA.onStart([]() {});
  ArduinoOTA.onEnd([]() {});
  ArduinoOTA.onError([](ota_error_t error) {
    (void)error;
    ESP.restart();
  });
  ArduinoOTA.begin();

  SPI.begin(); // Init SPI bus
  rfid.PCD_Init(); // Init MFRC522
  rfid.PCD_SetAntennaGain(rfid.RxGain_max);

  strcat_P(responTopic, clientID);
  strcat_P(uidTopic, clientID);
  strcat_P(statusTopic, clientID);
  strcat_P(lockTopic, clientID);
  strcat_P(doorTopic, clientID);
  mqtt.setClient(wemos);
  mqtt.setServer(broker, port);
  if (auth == 1) {
    mqtt.connect(clientID, username, password, statusTopic, 2, 0, "0");   //broker akan mengirim will message "0" (disconnect) ke client lain yg subscribe ke topic ini jika node ini disconnect
  }
  else {
    mqtt.connect(clientID, statusTopic, 2, 0, "0");
  }
  mqtt.setCallback(callback);
  mqtt.publish(statusTopic, "1"); //kirim status "1"=CONNECT
  mqtt.subscribe(responTopic);
  mqtt.subscribe("PING");
  mqtt.subscribe("TIME");
  mqtt.subscribe(lockTopic);

  lcd.clear();
  //lcd.noBacklight();

  Scheduler.start(&ota_loop);
  Scheduler.start(&mqtt_loop);
  Scheduler.start(&main_loop);
  Scheduler.start(&button_loop);
  Scheduler.start(&solenoid_loop);
  Scheduler.start(&buzzer_loop);
  Scheduler.start(&screen_loop);
  SCREEN = 1;
  BUZZER = 1;
  Scheduler.begin();
}

void loop() {}

void callback(char* topic, byte* payload, uint16_t len) {
  String payloadStr = "";
  for (uint16_t i = 0; i < len; i++) {
    payloadStr += char(payload[i]);
  }
  //int value = payloadStr.toInt();
  if (strcmp_P(topic, responTopic) == 0) {  //jika dapat message di responTopic
    //strcpy_P(TOPIC, topic);
    receiveTime = millis() - sendTime;  //get response time for authentication flow
    RESPON = payloadStr;
  }
  if (strcmp_P(topic, "PING") == 0 && payloadStr == "ping") { //jika dapat message "ping" di topic "PING"
    mqtt.publish(statusTopic, "1"); //kirim status "1"=CONNECT
  }
  if (strcmp_P(topic, "TIME") == 0) {   //jika dapat message di topic "TIME"
    TIME = payloadStr;  //update waktu
  }
  if (strcmp_P(topic, lockTopic) == 0) {    //remote button/topic utk kontrol solenoid
    LOCK = payloadStr;
    SCREEN = 1;
  }
}

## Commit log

2020-05-11 PCB & Case
    PCB: eagle file
    Case: corel draw
    [absensi_wemos.brd, absensi_wemos.sch]
2020-05-11 Arduino code
2020-05-18 Version 1.0
    release v1.0: Node Monitor & Employee Manager (GUI) and Node firmware (Arduino: Wemos D1 Mini)
2020-06-03 -bug fix on authentication process (timeout and response)
    [S.C.A.N_OTA.ino]
2020-07-14 Fix stability & memory issue
    -use '' instead of str() to increase stability
    -add configurable variable, fix overflow memory issue
    [S.C.A.N_OTA.ino]
2020-07-21 Update S.C.A.N_OTA.ino
    -MQTT server parameter is configurable on line 26 to 31
    -OTA server parameter is configurable on line 33 to 34
    -tested by me until 12 hours long (hope it's working for 24/7 nonstop) - ALWAYS MEMORY PROBLEM... ALWAYS...
    [S.C.A.N_OTA.ino]

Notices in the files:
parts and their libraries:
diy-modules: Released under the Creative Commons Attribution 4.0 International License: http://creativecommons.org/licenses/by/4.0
